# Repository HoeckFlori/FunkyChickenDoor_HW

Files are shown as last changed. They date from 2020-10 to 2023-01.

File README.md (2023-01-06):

# FunkyChickenDoor_HW

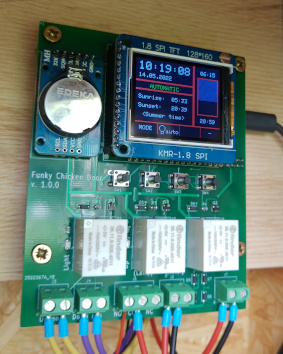
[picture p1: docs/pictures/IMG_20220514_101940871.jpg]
Hardware in mounting position


In this repository the **electronic hardware** for the 'Funky Chicken Door' [project](https://github.com/HoeckFlori/FunkyChickenDoor_SW) is/was developed.

The idea is, to develop a automatic chicken-house-door-controller and provide it on a semi-professional level with simple, available and inexpensive components. For detailed information about the features, the usage and anything else, have a look into the [corresponding software repo](https://github.com/HoeckFlori/FunkyChickenDoor_SW).

The circuit diagrams and PCB is drawn with [KiCad](https://kicad.org/) and can be opened and edited at any time with it.

You can build up the hardware as strip board solution or order a PCB from your preferred PCB dealer.  

<details>
  <summary>'development stripboard solution'</summary>

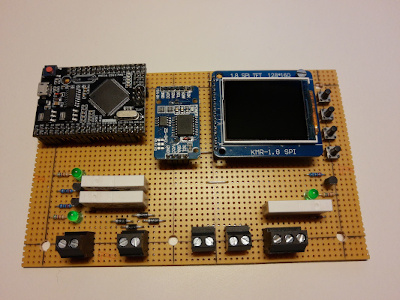
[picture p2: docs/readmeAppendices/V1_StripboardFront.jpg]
front


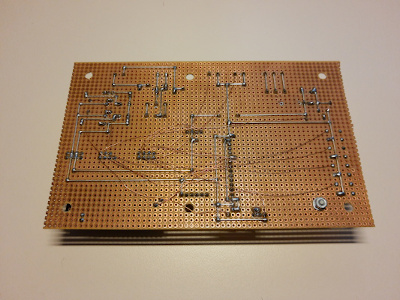
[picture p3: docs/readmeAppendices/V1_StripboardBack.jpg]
back

</details>

If you want want to use the hardware you can rebuild it for your private stuff. A BOM with the order codes to an German electronic distributor is attached. Nevertheless some 'specialized' components are needed. Look below.

In case of problems, errors or suggestions for improvement, please send me an issue.

# Quick links within the repository
## KiCad project
[KiCadProject](./AMShieldV1/ChickenDoor_V1.pro)

## Schematic
[Schematic](./AMShieldV1/ChickenDoor_V1_1-0-0_Schematic.pdf)

## Assembly print
[Assembly print](./AMShieldV1/ChickenDoor_V1_1-0-0_AssemblyPrint.pdf)

## BOM (bill of materials)
[Schematic](./AMShieldV1/ChickenDoor_V1_1-0-0_BOM_withReicheltOrderCodes.ods)

## Pictures of the PCB
<details>
  <summary>Click me to see some screenshots</summary>
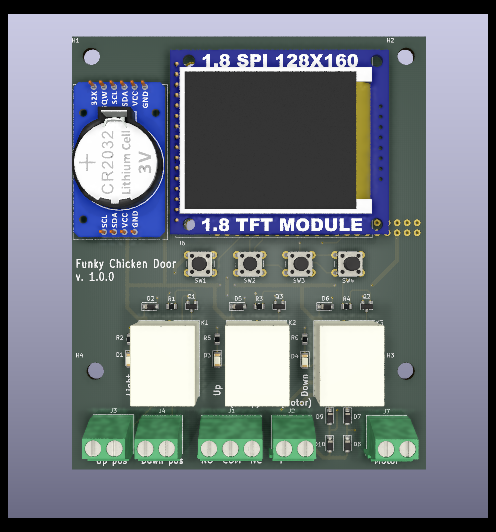
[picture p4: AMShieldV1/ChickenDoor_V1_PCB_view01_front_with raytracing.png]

  
![](./AMShieldV1/ChickenDoor_V1_PCB_view02_side%20right.png
  
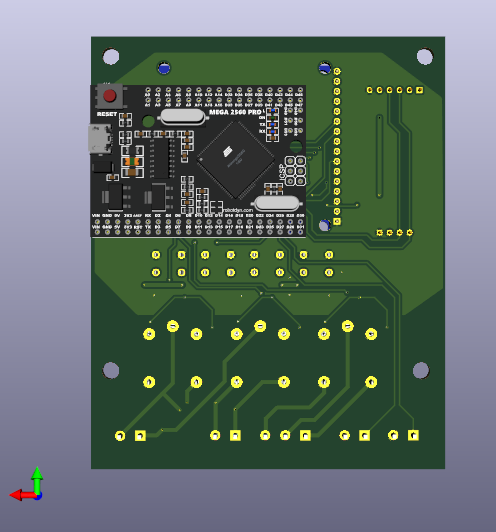
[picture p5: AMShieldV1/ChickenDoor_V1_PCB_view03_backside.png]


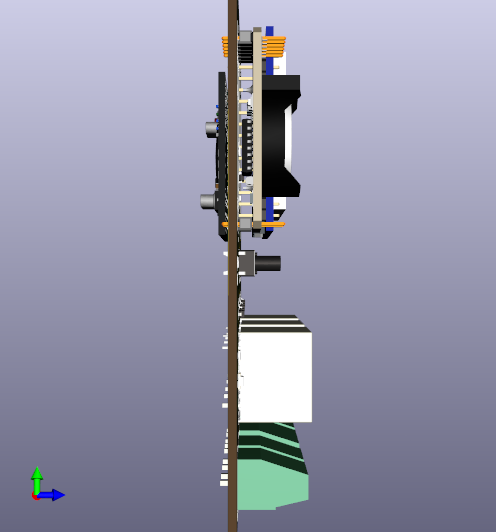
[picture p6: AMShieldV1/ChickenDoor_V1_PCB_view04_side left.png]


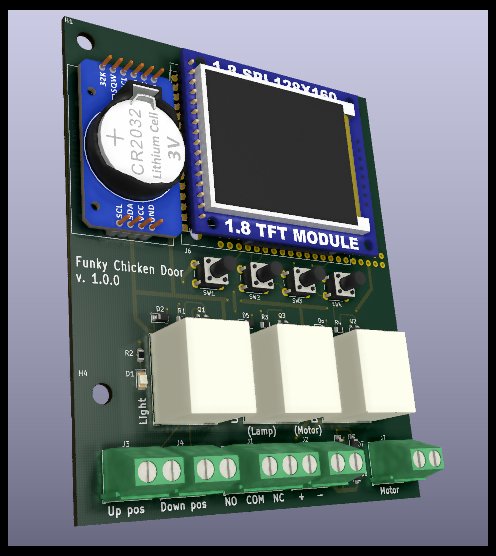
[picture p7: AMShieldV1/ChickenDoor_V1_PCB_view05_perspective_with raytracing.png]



</details>

## The more 'specialized' components you need to get

<details>
  <summary>'click me to open the list'</summary>

| What | Link to further information and (possible) vendors | Detailed information | Realistic price (from a well-known auction platform with longer shipping time), mid 2020 |
| --- | --- | --- | --- |
| MCU Board 'Mega 2560 PRO (Embed) CH340G/ATmega2560-16AU' | [https://robotdyn.com/mega-2560-pro-embed-ch340g-atmega2560-16au.html](https://robotdyn.com/mega-2560-pro-embed-ch340g-atmega2560-16au.html) or [https://www.reichelt.de/at/en/arduino-compatible-mega-2560-pro-board-ard-mega2560-pro-p299355.html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](https://www.reichelt.de/at/en/arduino-compatible-mega-2560-pro-board-ard-mega2560-pro-p299355.html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) | <ul><li>[Dimensional drawing](https://robotdyn.com/pub/media/0G-00005641==MEGA-PRO-CH340GATmega2560/DOCS/DIM==0G-00005641==MEGA-PRO-CH340GATmega2560.pdf)</li><li>[Input and Output I/O diagram](https://robotdyn.com/pub/media/0G-00005641==MEGA-PRO-CH340GATmega2560/DOCS/PINOUT==0G-00005641==MEGA-PRO-CH340GATmega2560.pdf)</li><li>[Schematic](https://robotdyn.com/pub/media/0G-00005641==MEGA-PRO-CH340GATmega2560/DOCS/Schematic==0G-00005641==MEGA-PRO-CH340GATmega2560.pdf)</li></ul> | ~ 7,- € |
| RTC DS3231 I2C AT24C32 Real Time Clock | https://www.makershop.de/module/rtc/rtc-ds3231-i2c/ | [Interface DS3231 Precision RTC Module with Arduino](https://lastminuteengineers.com/ds3231-rtc-arduino-tutorial/) | ~ 3,- € |
| 1,8 Zoll TFT LCD Display Modul 128×160 | [https://www.amazon.com/HiLetgo-ST7735R-128160-Display-Arduino/dp/B00LSG51MM](https://www.amazon.com/HiLetgo-ST7735R-128160-Display-Arduino/dp/B00LSG51MM) or [https://www.makershop.de/display/lcd-tft/waveshare-1-8inch-lcd-modul/](https://www.makershop.de/display/lcd-tft/waveshare-1-8inch-lcd-modul/) | Try to get a display like in the link! The market is full of displays of this type, but each one has other connectors, dimensions, orientations, ... .<br/> Some may interesting links:<br/> [1.8" Serial SPI 128x160 Color TFT LCD Module Display](https://www.openhacks.com/uploadsproductos/tutorial_display_tft.pdf),<br/> [https://learn.adafruit.com/1-8-tft-display/breakout-pinouts](https://learn.adafruit.com/1-8-tft-display/breakout-pinouts),<br/> [Arduino Tutorial: Making the KMR-1.8 SPI (TFT Display) work!](https://www.mschoeffler.de/2019/06/20/arduino-tutorial-making-the-kmr-1-8-spi-tft-display-work/) | ~ 8,-€ <br/> (on a well-known internet auction house) |

</details>

# FAQ
Currently nothing :smiley:

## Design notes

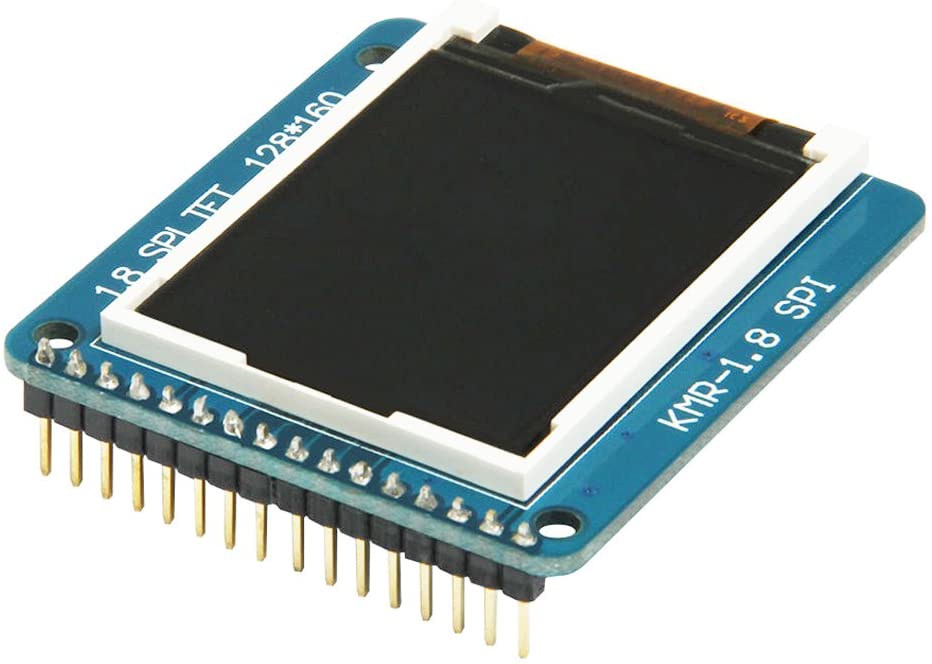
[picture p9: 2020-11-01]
docs/displayTemp/61+4ZxjomVL._AC_SL1010_.jpg

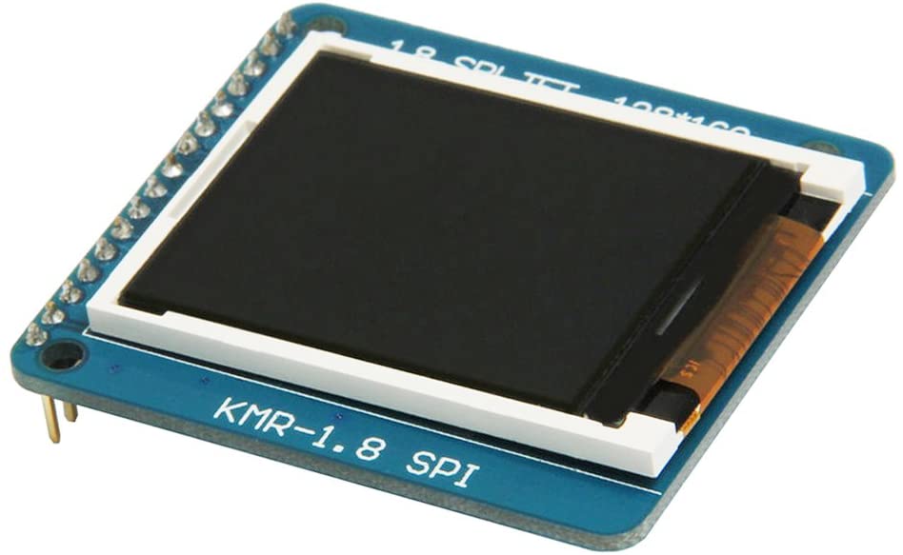
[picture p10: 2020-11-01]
docs/displayTemp/61WNY7D33nL._AC_SL1010_.jpg

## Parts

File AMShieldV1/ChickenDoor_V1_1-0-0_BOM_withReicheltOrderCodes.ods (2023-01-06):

ID | Bezeichner | Gehäuse | Stückzahl | Bezeichnung | Anbieter und Referenz | Bestellt | Reichelt Bestellnummer
1 | JP4,JP3,JP2,JP1 | SolderJumper-2_P1.3mm_Bridged_RoundedPad1.0x1.5mm | 4 | SolderJumper_2_Bridged
2 | J6 | KMR-1.8-SPI | 1 | KMR-1.8 SPI
3 | J7,J4,J3,J2 | TerminalBlock_Phoenix_MKDS-1,5-2-5.08_1x02_P5.08mm_Horizontal | 4 | Screw_Terminal_01x02 |  | x | LAKL 1,5 2 5,08
4 | J1 | TerminalBlock_Phoenix_MKDS-1,5-3-5.08_1x03_P5.08mm_Horizontal | 1 | Screw_Terminal_01x03 |  | x | LAKL 1,5 3 5,08
5 | U1 | MODULE_MEGA_PRO_EMBED_CH340G___ATMEGA2560 | 1 | MEGA_PRO_EMBED_CH340G___ATMEGA2560
6 | U2 | MODULE_TC00500_FHk_BatteryUpside | 1 | TC00500
7 | R7,R9,R4,R3,R1 | R_0805_2012Metric | 5 | 2k2 |  | x | SMD-0805 2,20K
8 | Q4 | SOT-23 | 1 | BC807 |  | x | BC 807 NXP
9 | D4,D3,D1 | LED_1206_3216Metric | 3 | LED |  |  | WUE 150120GS750
10 | Q3,Q2,Q1 | SOT-23 | 3 | BC817 |  | x | BC 817 NXP
11 | D6,D5,D2,D10,D9,D8,D7 | D_SOD-123 | 7 | 1N4448W |  | x | 1N 4448W DIO
12 | R8 | R_0805_2012Metric | 1 | 18R |  | x | SMD-0805 18,0
13 | R6,R5,R2 | R_0805_2012Metric | 3 | 560 |  | x | SMD-0805 560
14 | H4,H3,H2,H1 | MountingHole_4.3mm_M4_DIN965 | 4 | MountingHole
15 | K3,K2,K1 | Relay_SPDT_Finder_36.11 | 3 | FINDER-36.11 |  | x | FIN 36.11 5V
16 | SW4,SW3,SW2,SW1 | SW_PUSH_6mm_H9.5mm | 4 | SW_Push |  | x | TASTER 3301B

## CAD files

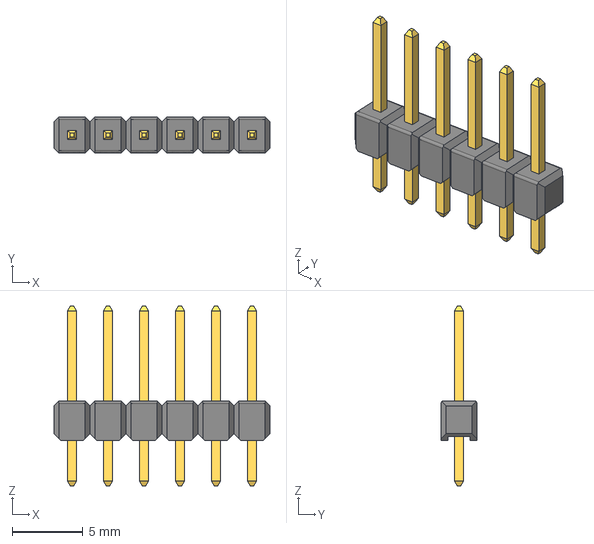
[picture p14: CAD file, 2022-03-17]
cadModels/Pin Header 1x6 TH Pitch 2.54mm.stp
15.2 x 2.54 x 12.7 mm

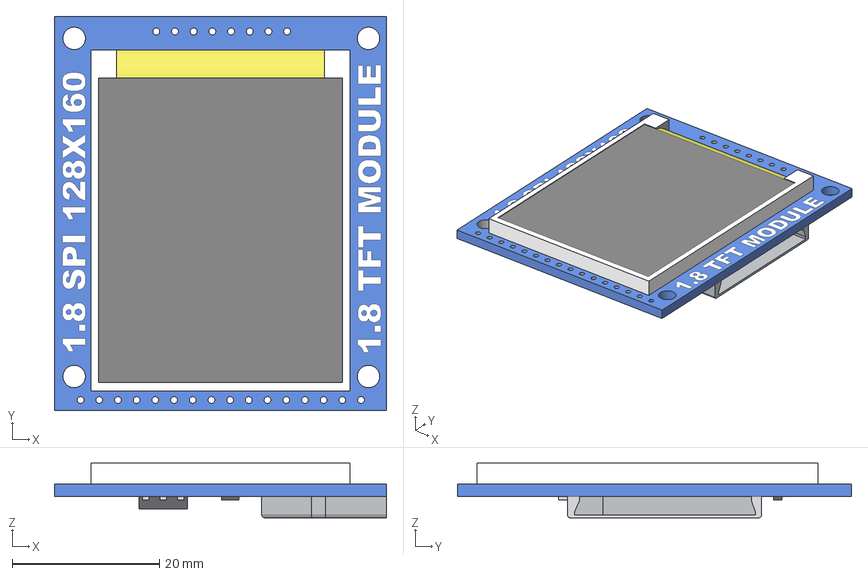
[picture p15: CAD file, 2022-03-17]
cadModels/1.8 LCD.stp
45.1 x 53.5 x 7.42 mm

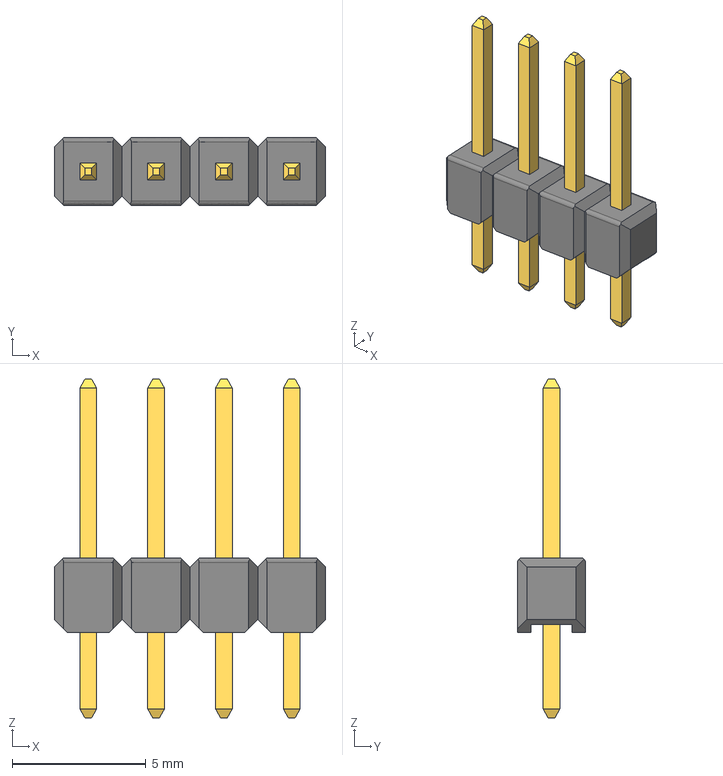
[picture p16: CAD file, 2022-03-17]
cadModels/Pin Header 1x4 TH Pitch 2.54mm.stp
10.2 x 2.54 x 12.7 mm

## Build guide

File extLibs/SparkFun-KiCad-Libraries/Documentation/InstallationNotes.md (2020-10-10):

Installation Notes
----------------

* [The KiCad site](http://kicad-pcb.org/)

**KiCad installation**

* Uninstall previous versions of KiCad
* Download KiCad stable version 4.0.5 from [http://kicad-pcb.org/download/](http://kicad-pcb.org/download/windows/) and install
* After install, you'll be prompted to install "Wings 3D", check this box to be redirected to [http://www.wings3d.com/](http://www.wings3d.com/)
* Download and install the stable release 2.1.5

**Using the libraries**

* Create a local project (this is necessary because projects hold library path information)
* Open the "Schematic Library Editor"
* Prefrences -> Component Libraries
  * Remove all libraries from list
  * Add -> navigate to SparkFun-KiCad-Libraries -> select all .lib files -> open, then hit OK
  * Test by selecting an active library.  All sparkfun libraries should be displayed.  Close the library editor
* Open the "PCB Footprint Editor"
* Preferences -> Footprint Library Manager
  * Remove all (if any) libraries, hit OK
* Preferences -> Footprint Libraries Wizard
  * Next (files on my computer)
  * Navigate to SparkFun-KiCad-Libraries -> select all .mod files and hit ok
  * Next
  * Select for this project only
  * Next
  * Close the editor
* Save the project (Green arrow into extern HDD icon, no menu exists)

Now, this project is linked to the libraries.  Open a schematic and place components.  See KiCad enginursday post for converting from schematic into board (Note: You need to have nets for this to work... not just unconnected components)

**License Information**

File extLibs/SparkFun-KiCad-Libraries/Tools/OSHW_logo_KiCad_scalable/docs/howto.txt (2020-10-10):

How to make your own:
---------------------

Watch / read this first:

* http://www.kicad-pcb.org/display/KICAD/Videos+by+zupnikal

The last two videos should be helpful for how to create a custom .emp file from images.

* http://www.re-innovation.co.uk/web12/index.php/en/blog-75/230-adding-logo-to-kicad

If you use linux (which you should), you don't have to use the online-scaler. Just use the scripts!

---

* Create a folder to hold your new footprint library.
* Copy the scripts 'make_lib.sh' and 'scale.pl' into that folder.
* Make sure these files are executable (chmod u+x ...).
* Copy your custom .emp file into that foler.

* Run the 'make_lib.sh' script as follows:

./make_lib.sh input-file.emp lib-name.mod START END

START and END are placeholders for positive integer numbers (1,2,3...) that determine
the range of created footprint sizes. The units are metric (mm).

The 'lib-name.mod' file will show up in the 'lib' sub-folder. Add it to your pcbnew
library settings as usual.

Footprints that are created for back-layers are automagically mirrored horizontally.
To place them onto a back-layer, hover the mouse-pointer over them and press 'f' for 'flip'.

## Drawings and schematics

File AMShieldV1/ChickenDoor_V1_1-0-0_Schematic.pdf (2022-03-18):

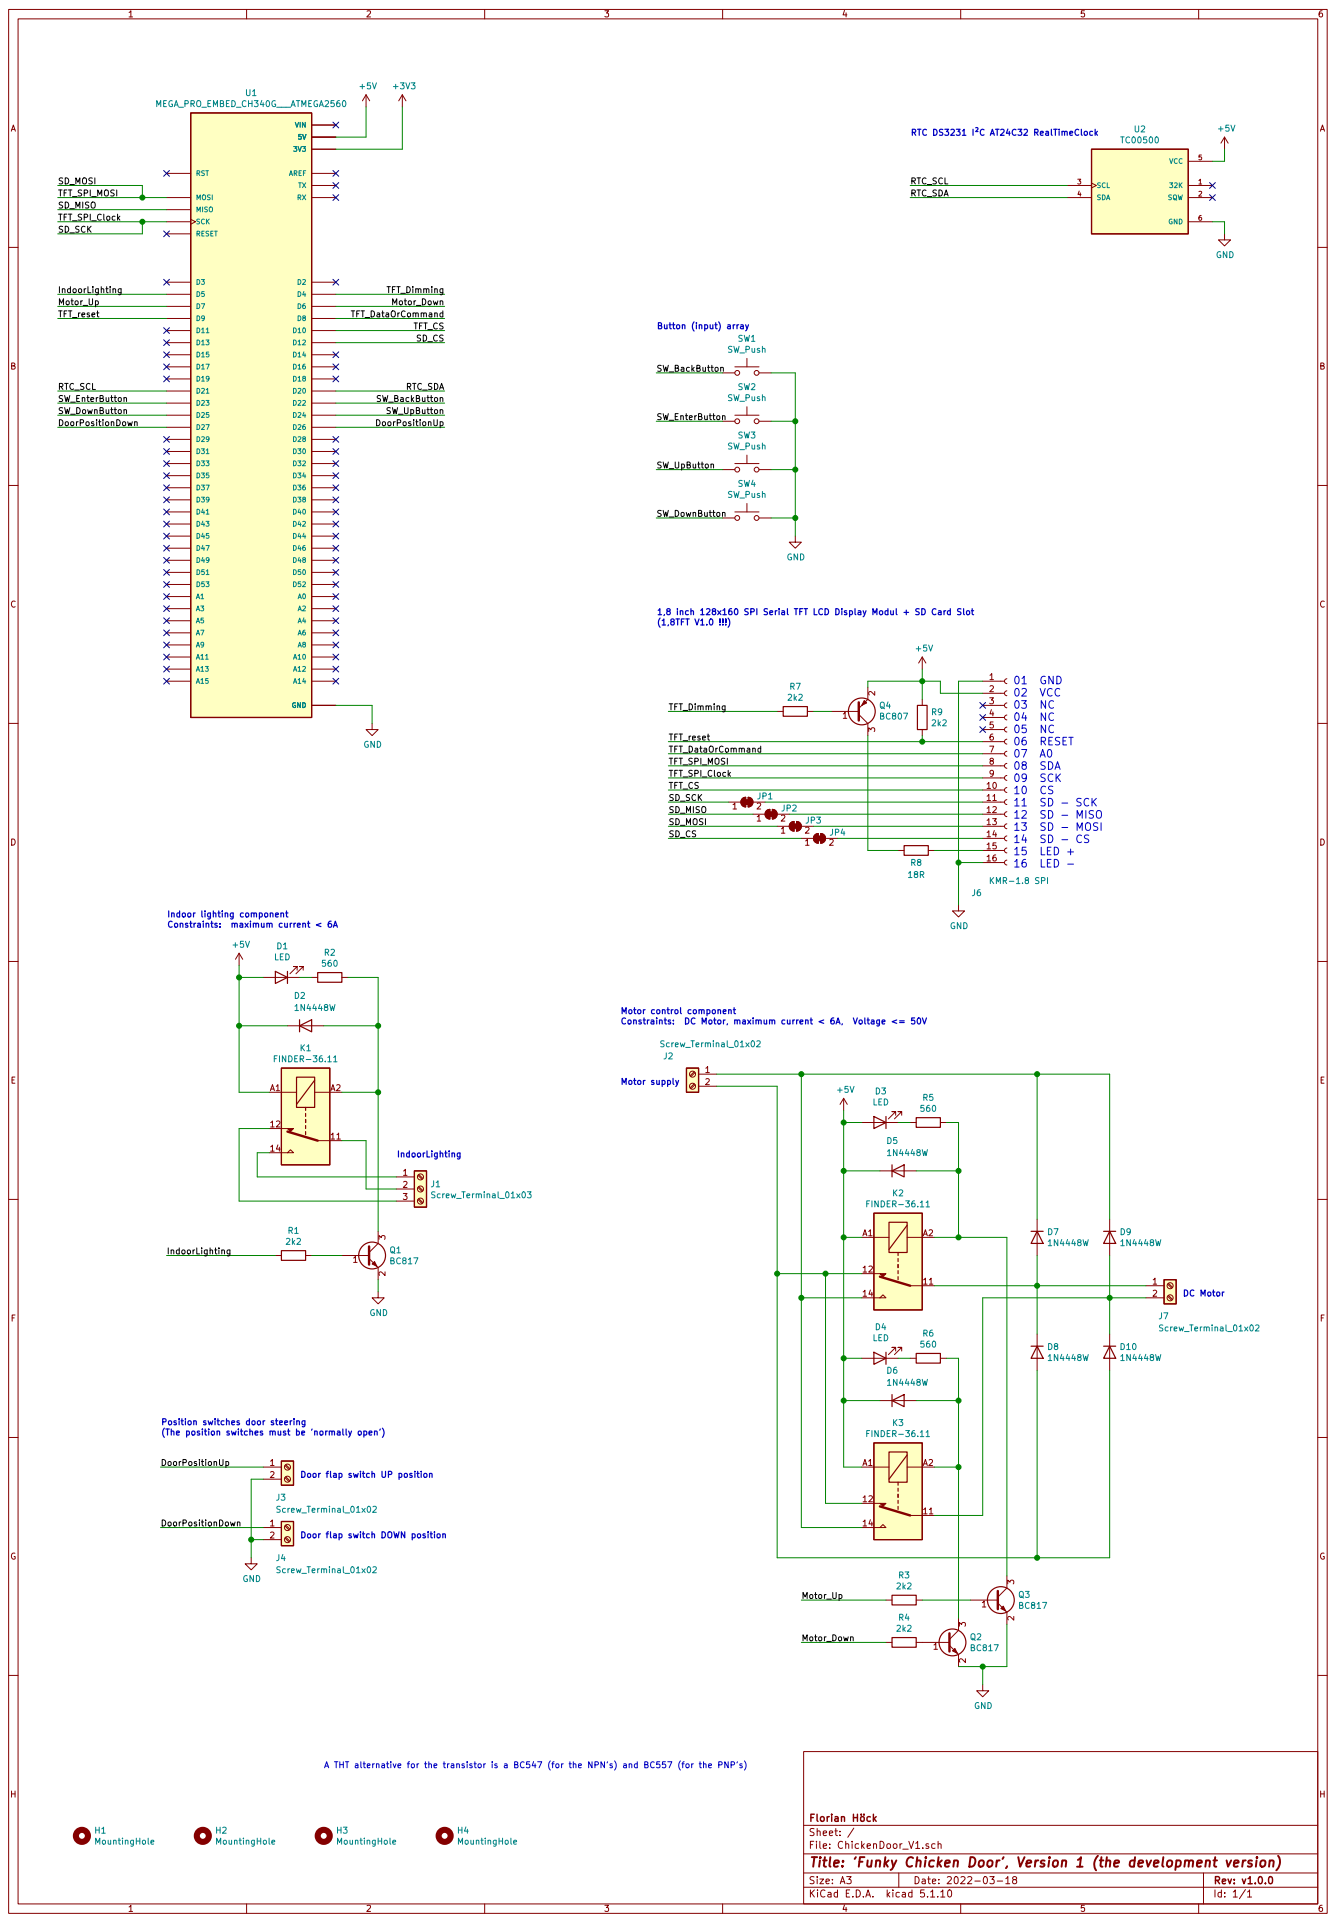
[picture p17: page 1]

1,8 inch 128x160 SPI Serial TFT LCD Display Modul + SD Card Slot
(1,8TFT V1.0 !!!)

Motor control component
Constraints: DC Motor, maximum current < 6A, Voltage <= 50V

Position switches door steering
(The position switches must be 'normally open')

A THT alternative for the transistor is a BC547 (for the NPN's) and BC557 (for the PNP's)

File: ChickenDoor_V1.sch Sheet: / Florian Höck

Id: 1/1 Title: 'Funky Chicken Door', Version 1 (the development version)

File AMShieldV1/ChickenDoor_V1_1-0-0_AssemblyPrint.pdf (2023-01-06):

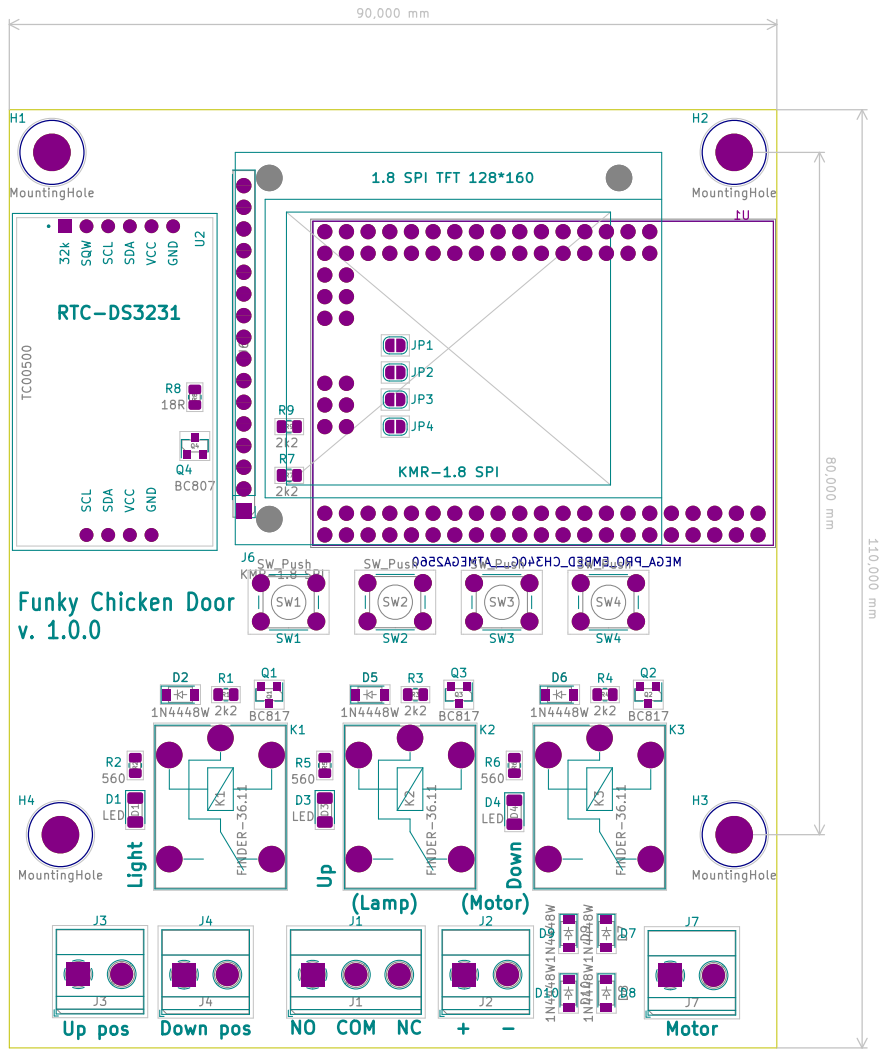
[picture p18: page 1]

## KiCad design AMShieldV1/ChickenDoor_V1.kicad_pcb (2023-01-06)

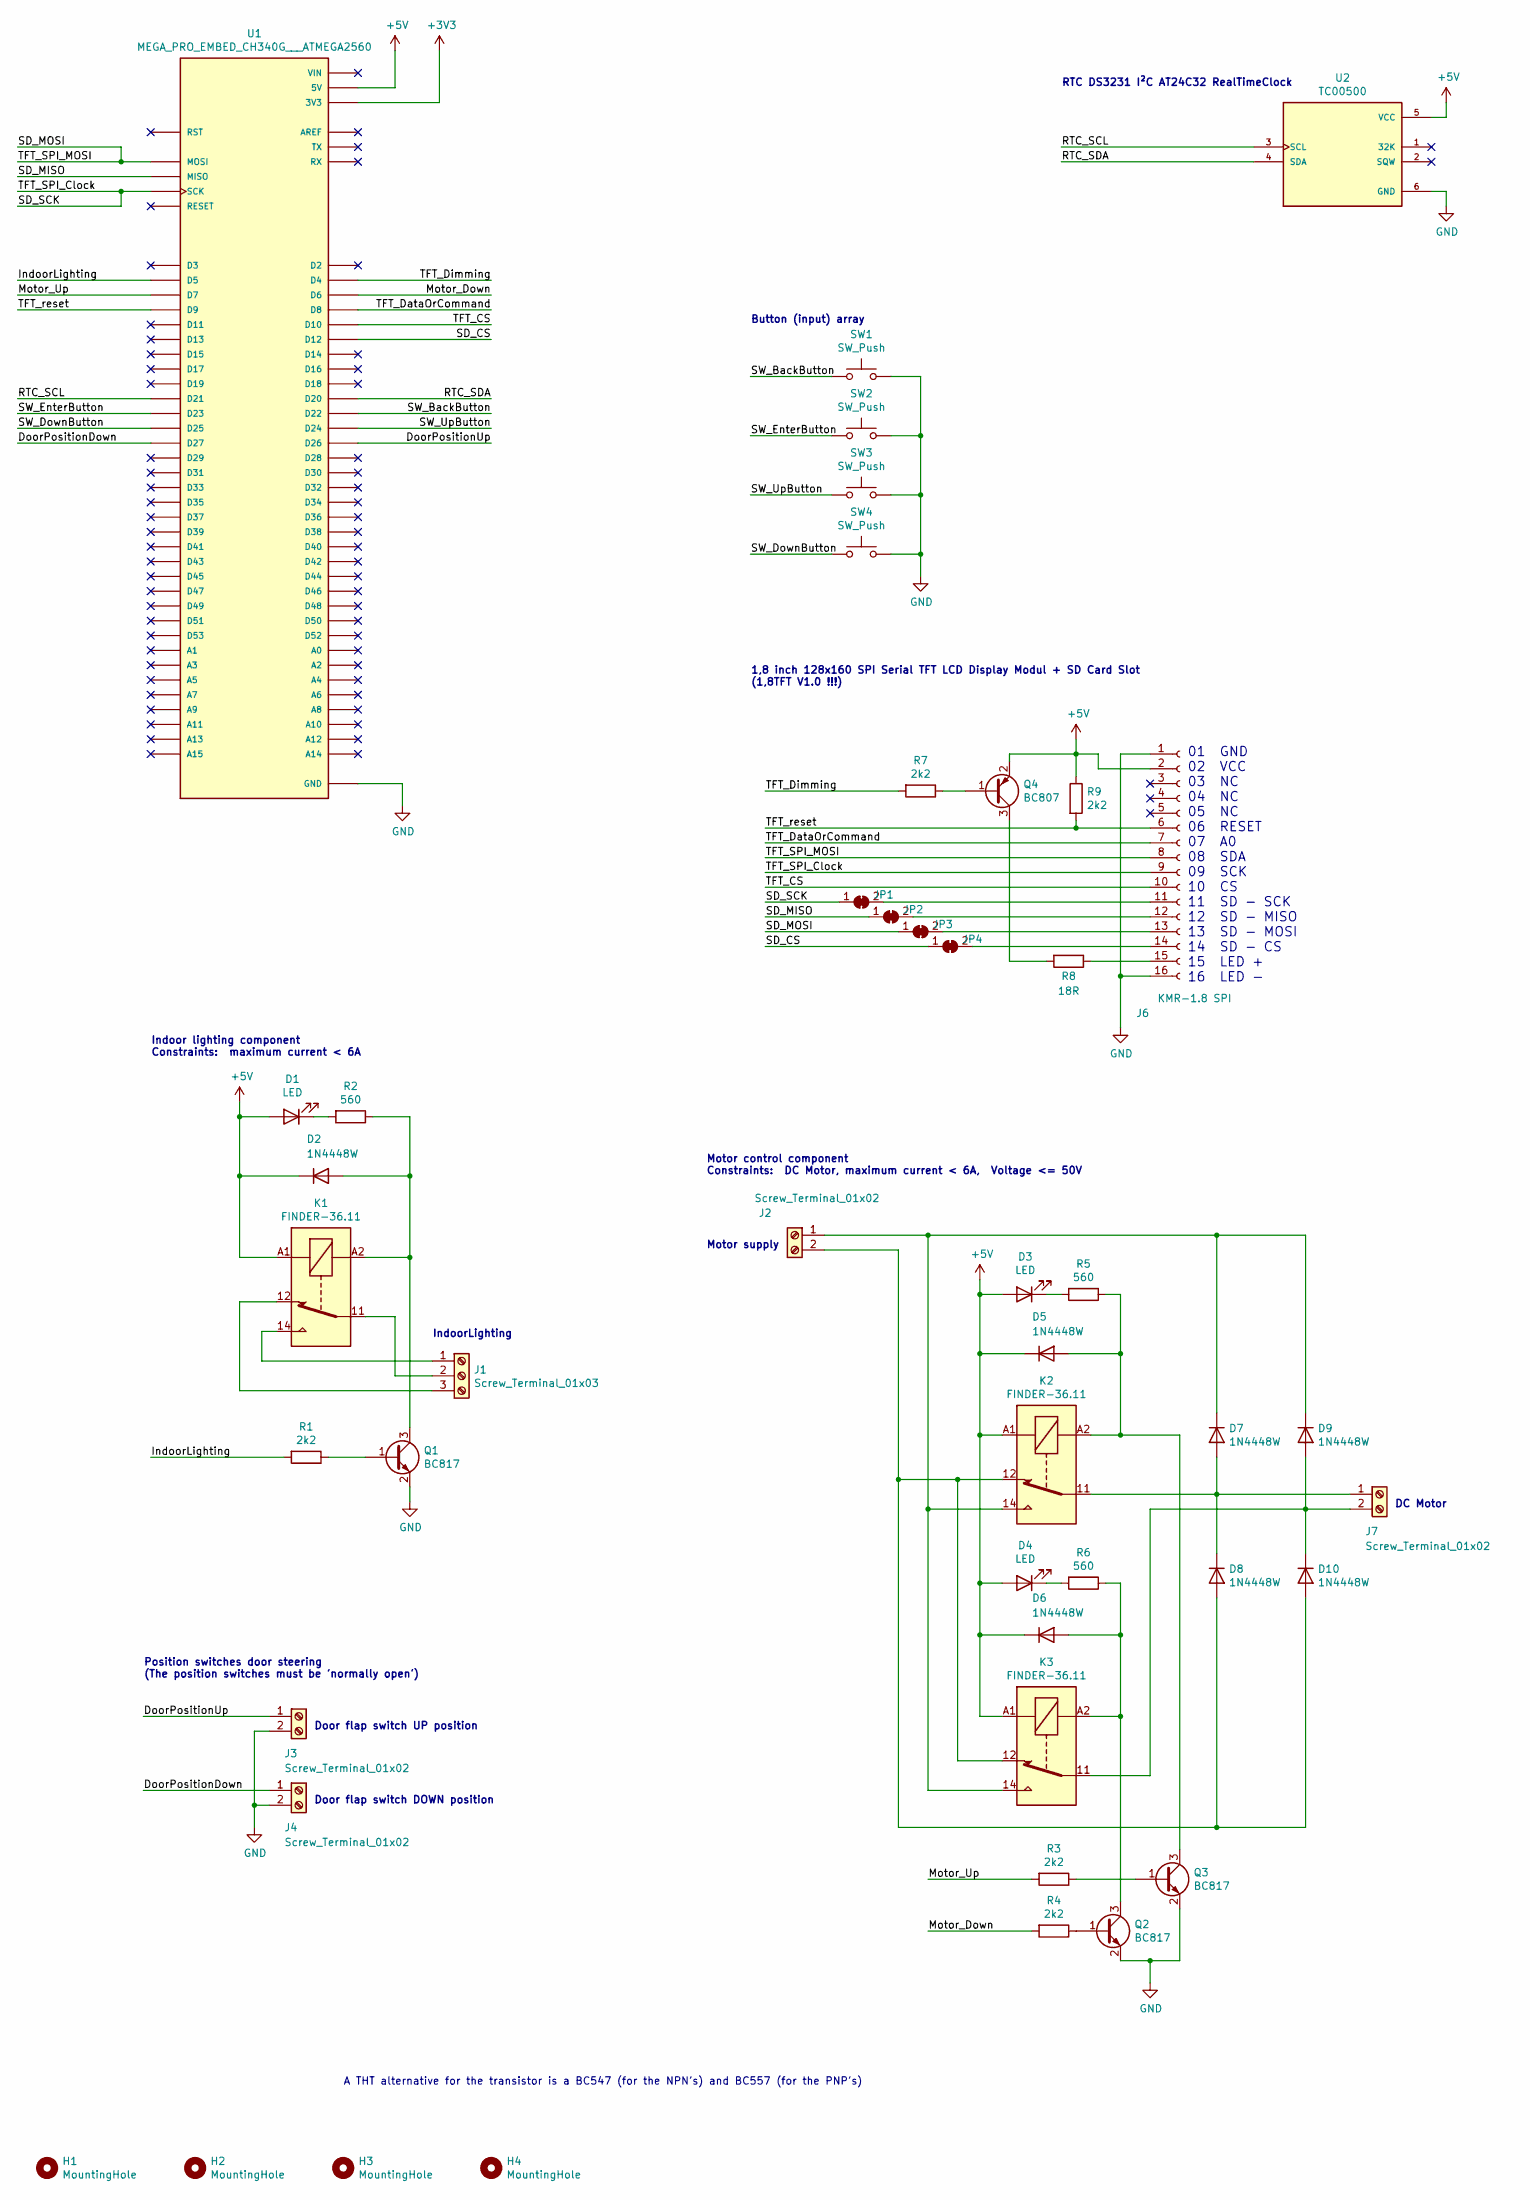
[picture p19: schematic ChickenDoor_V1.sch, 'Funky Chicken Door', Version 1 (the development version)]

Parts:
D1, D3, D4: LED; LED_1206_3216Metric
D2, D5, D6, D7, D8, D9, D10: 1N4448W; D_SOD-123
H1, H2, H3, H4: MountingHole; MountingHole_4.3mm_M4_DIN965
J1: Screw_Terminal_01x03; TerminalBlock_Phoenix_MKDS-1,5-3-5.08_1x03_P5.08mm_Horizont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
J2, J3, J4, J7: Screw_Terminal_01x02; TerminalBlock_Phoenix_MKDS-1,5-2-5.08_1x02_P5.08mm_Horizont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
J6: KMR-1.8 SPI; KMR-1.8-SPI
JP1, JP2, JP3, JP4: SolderJumper_2_Bridged; SolderJumper-2_P1.3mm_Bridged_RoundedPad1.0x1.5mm
K1, K2, K3: FINDER-36.11; Relay_SPDT_Finder_36.11
Q1, Q2, Q3: BC817; SOT-23
Q4: BC807; SOT-23
R1, R3, R4, R7, R9: 2k2; R_0805_2012Metric
R2, R5, R6: 560; R_0805_2012Metric
R8: 18R; R_0805_2012Metric
SW1, SW2, SW3, SW4: SW_Push; SW_PUSH_6mm_H9.5mm
U1: MEGA_PRO_EMBED_CH340G___ATMEGA2560; MODULE_MEGA_PRO_EMBED_CH340G___ATMEGA2560; PARTREV 12/May/2017
U2: TC00500; MODULE_TC00500_FHk_BatteryUpside; PARTREV N/A

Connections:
+3V3: U1.3V3_1 (3V3), U1.3V3_2 (3V3)
+5V: D1.2 (A), D2.1 (K), D3.2 (A), D4.2 (A), D5.1 (K), D6.1 (K), J6.2, K1.A1, K2.A1, K3.A1, Q4.2 (E), R9.1, U1.5V_1 (5V), U1.5V_2 (5V), U1.5V_3 (5V), U2.5 (VCC)
/DoorPositionDown: J4.1, U1.D27
/DoorPositionUp: J3.1, U1.D26
/IndoorLighting: R1.2, U1.D5
/Motor_Down: R4.2, U1.D6
/Motor_Up: R3.2, U1.D7
/RTC_SCL: U1.D21, U2.3 (SCL)
/RTC_SDA: U1.D20, U2.4 (SDA)
/SD_CS: JP4.1 (A), U1.D12
/SD_MISO: JP2.1 (A), U1.MISO
/SD_MOSI: J6.8, JP3.1 (A), U1.MOSI
/SD_SCK: J6.9, JP1.1 (A), U1.SCK
/SW_BackButton: SW1.1, U1.D22
/SW_DownButton: SW4.1, U1.D25
/SW_EnterButton: SW2.1, U1.D23
/SW_UpButton: SW3.1, U1.D24
/TFT_CS: J6.10, U1.D10
/TFT_DataOrCommand: J6.7, U1.D8
/TFT_Dimming: R7.2, U1.D4
/TFT_reset: J6.6, R9.2, U1.D9
GND: J3.2, J4.2, J6.1, J6.16, Q1.2 (E), Q2.2 (E), Q3.2 (E), SW1.2, SW2.2, SW3.2, SW4.2, U1.GND_1 (GND), U1.GND_2 (GND), U1.GND_3 (GND), U2.6 (GND)
unnamed: D1.1 (K), R2.2
unnamed: D2.2 (A), K1.A2, Q1.3 (C), R2.1
unnamed: D3.1 (K), R5.2
unnamed: D4.1 (K), R6.2
unnamed: D5.2 (A), K2.A2, Q3.3 (C), R5.1
unnamed: D6.2 (A), K3.A2, Q2.3 (C), R6.1
unnamed: D7.1 (K), D9.1 (K), J2.1, K2.14, K3.14
unnamed: D7.2 (A), D8.1 (K), J7.1, K2.11
unnamed: D9.2 (A), D10.1 (K), J7.2, K3.11
unnamed: D8.2 (A), D10.2 (A), J2.2, K2.12, K3.12
unnamed: J1.1, K1.14
unnamed: J1.2, K1.11
unnamed: J1.3, K1.12
unnamed: J6.11, JP1.2 (B)
unnamed: J6.12, JP2.2 (B)
unnamed: J6.13, JP3.2 (B)
unnamed: J6.14, JP4.2 (B)
unnamed: J6.15, R8.1
unnamed: Q1.1 (B), R1.1
unnamed: Q2.1 (B), R4.1
unnamed: Q3.1 (B), R3.1
unnamed: Q4.1 (B), R7.1
unnamed: Q4.3 (C), R8.2
unnamed: U1.VIN_1 (VIN), U1.VIN_2 (VIN)

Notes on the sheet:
01 GND 02 VCC 03 NC 04 NC 05 NC 06 RESET 07 A0 08 SDA 09 SCK 10 CS 11 SD - SCK 12 SD - MISO 13 SD - MOSI 14 SD - CS 15 LED + 16 LED -
1,8 inch 128x160 SPI Serial TFT LCD Display Modul + SD Card Slot (1,8TFT V1.0 !!!)
RTC DS3231 I²C AT24C32 RealTimeClock
DC Motor
Motor supply
Door flap switch UP position
Door flap switch DOWN position
IndoorLighting
Button (input) array
Motor control component Constraints: DC Motor, maximum current < 6A, Voltage <= 50V
Indoor lighting component Constraints: maximum current < 6A
Position switches door steering (The position switches must be 'normally open')
A THT alternative for the transistor is a BC547 (for the NPN's) and BC557 (for the PNP's)

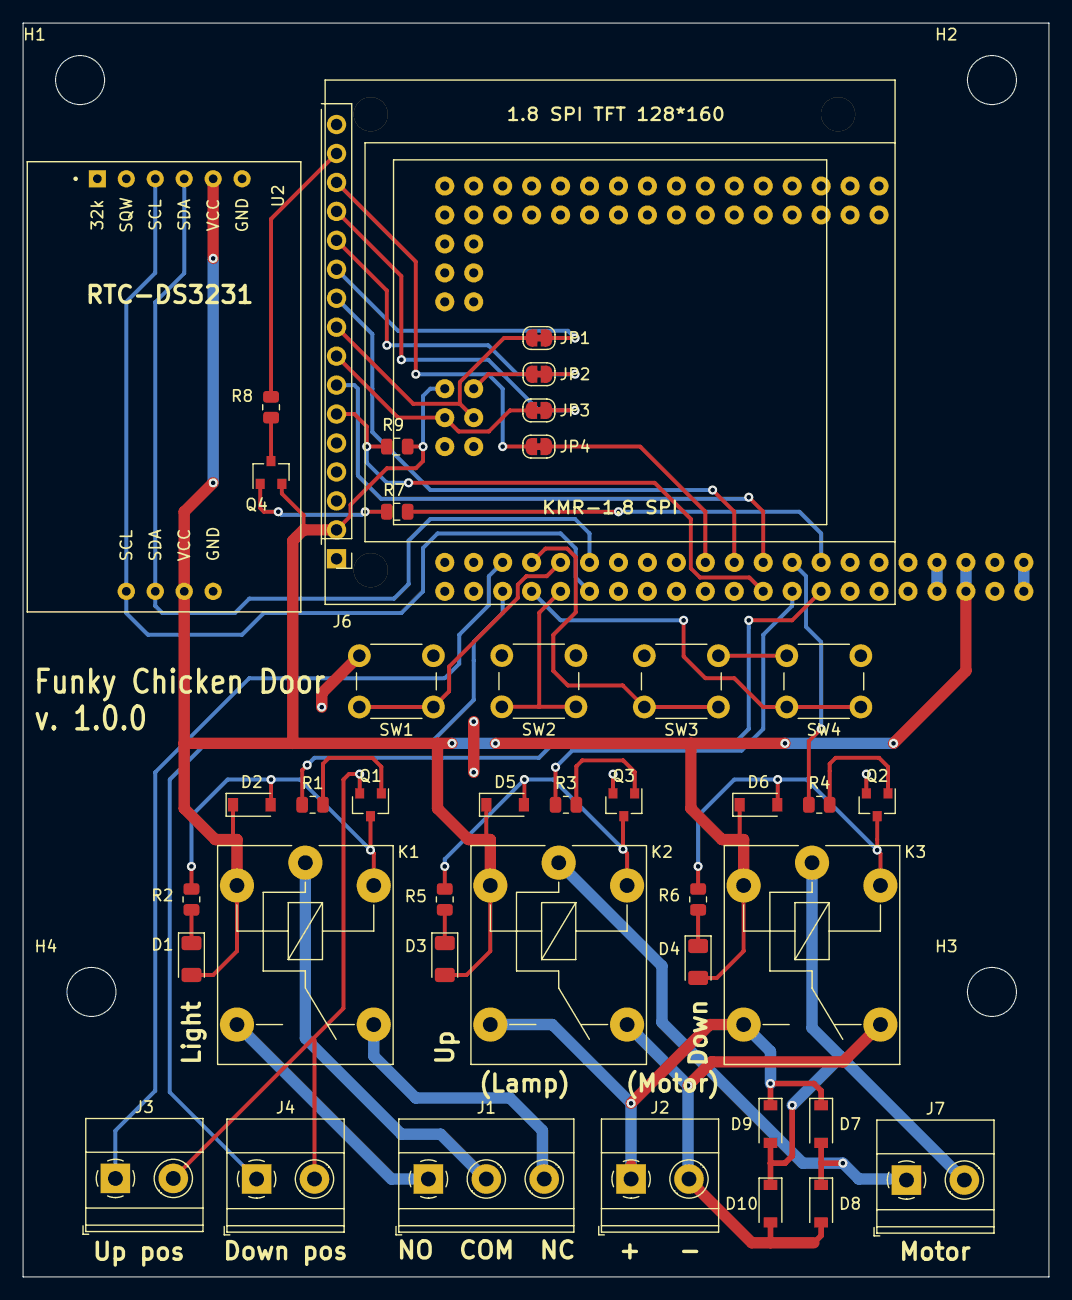
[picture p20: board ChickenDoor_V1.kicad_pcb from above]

Board: 2 copper layers, 90.0 x 110.0 mm, 46 parts (1 on the bottom side), 46 nets.

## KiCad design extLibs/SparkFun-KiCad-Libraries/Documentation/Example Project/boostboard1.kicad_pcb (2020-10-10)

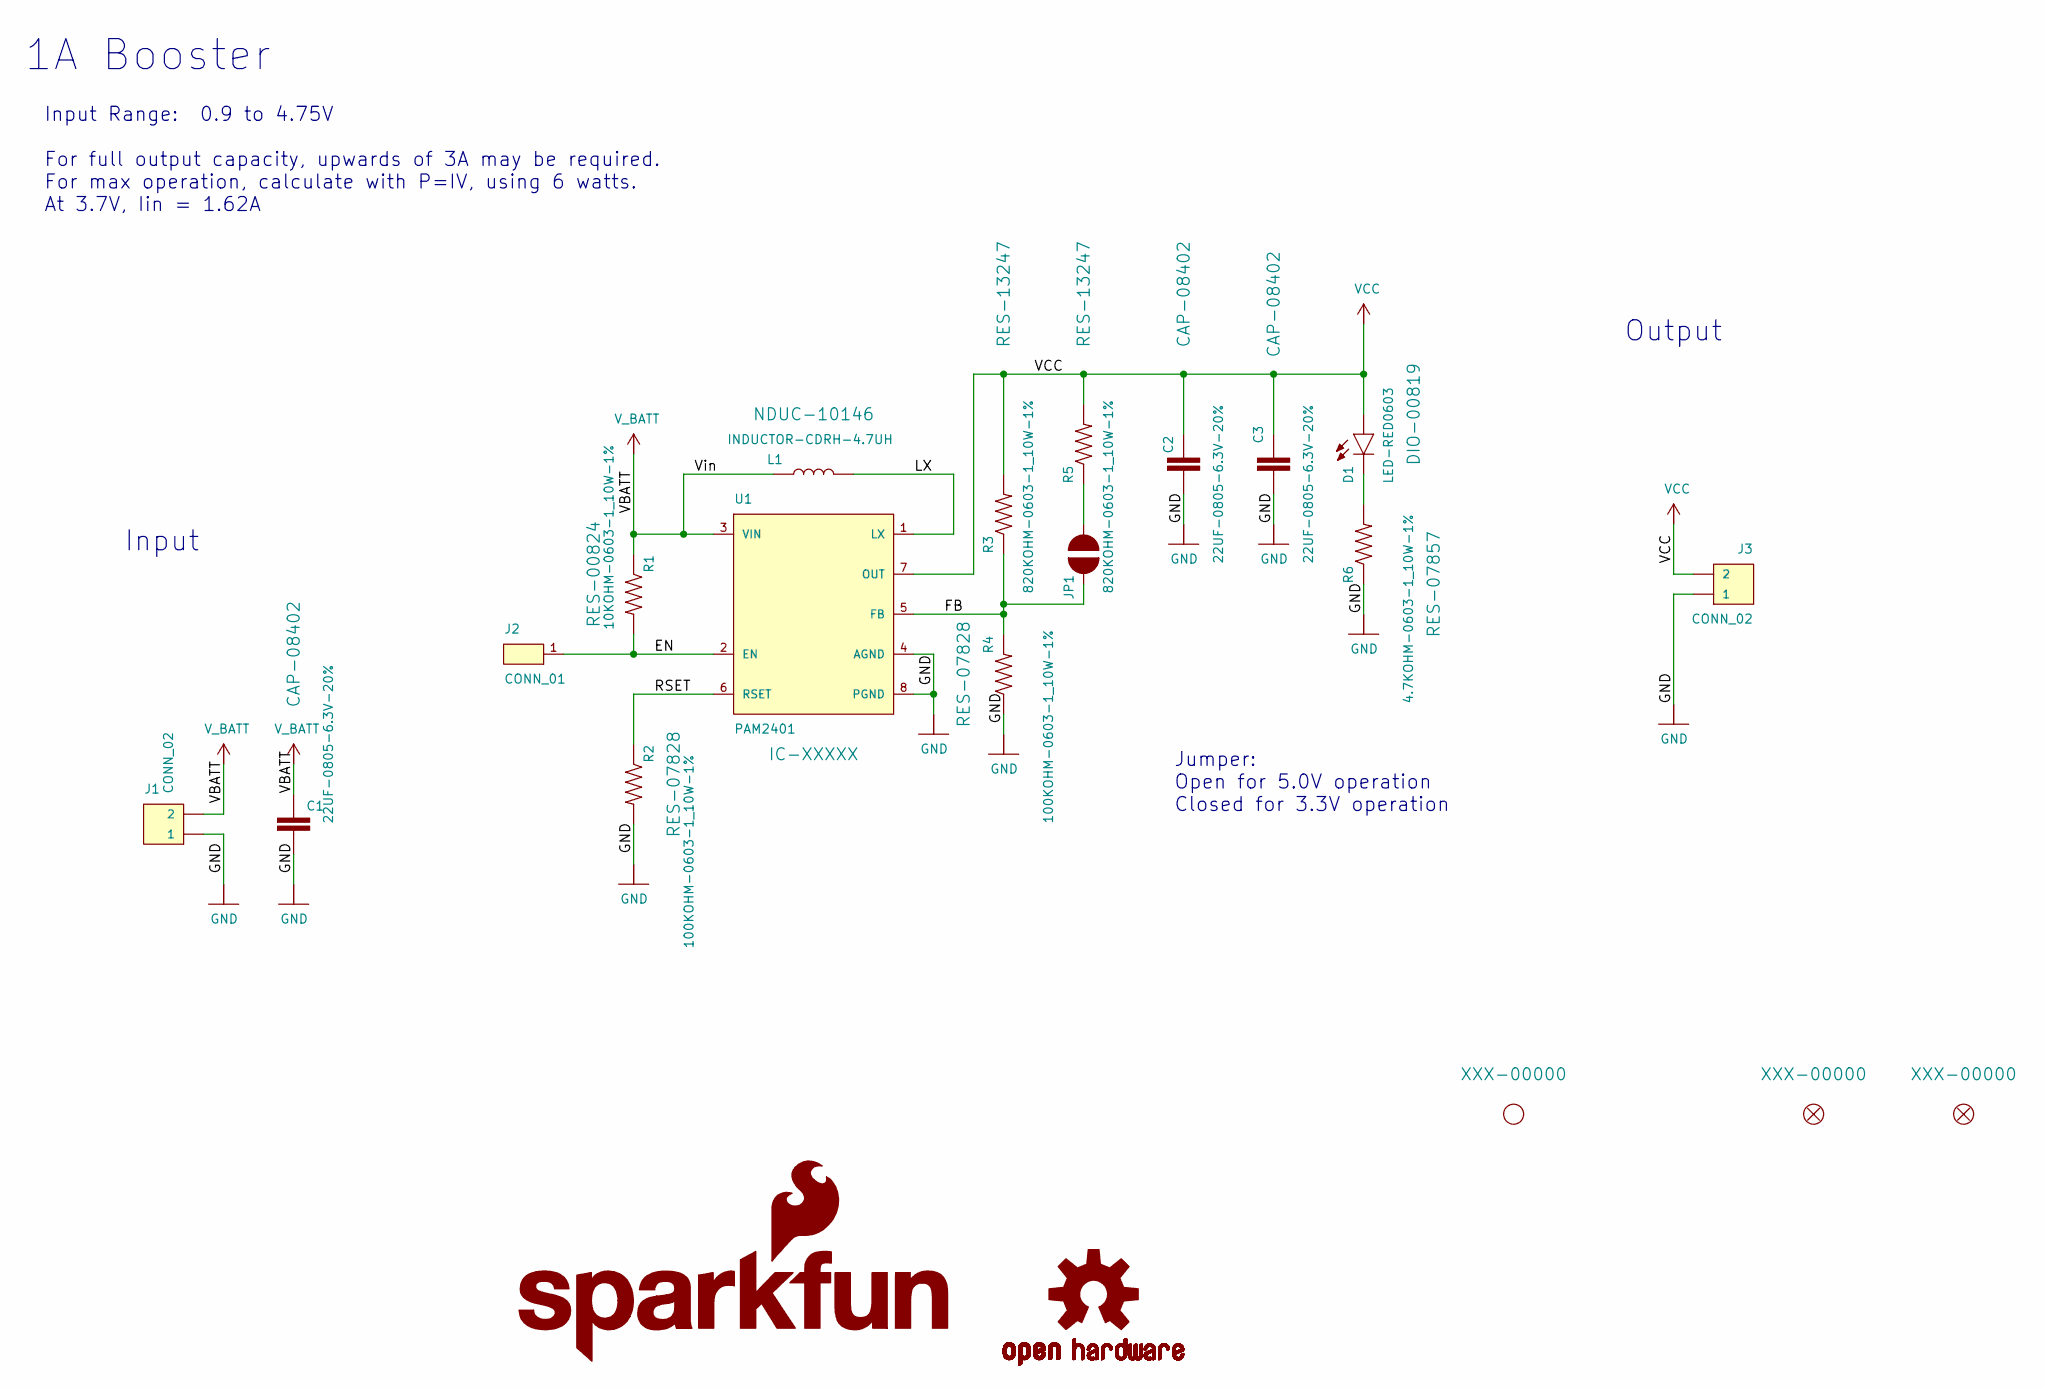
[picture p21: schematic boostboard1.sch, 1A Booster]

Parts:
C1, C2, C3: 22UF-0805-6.3V-20%; 0805
D1: LED-RED0603; LED-0603
FD1, FD2: FIDUCIAL1X2; FIDUCIAL-1X2
H1: STAND-OFF
J1, J3: CONN_02; 1X02
J2: CONN_01; 1X01
JP1: JUMPER-SMT_2_NO; SMT-JUMPER_2_NO_SILK
L1: INDUCTOR-CDRH-4.7UH; INDUCTOR_2.2UH
LOGO1: SFE_LOGO_NAME_FLAME.1_INCH; SFE_LOGO_NAME_FLAME_.1
LOGO2: OSHW-LOGOS; OSHW-LOGO-S
R1: 10KOHM-0603-1_10W-1%; 0603
R2, R4: 100KOHM-0603-1_10W-1%; 0603
R3, R5: 820KOHM-0603-1_10W-1%; 0603
R6: 4.7KOHM-0603-1_10W-1%; 0603
U1: PAM2401; MSOP8

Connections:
/EN: J2.1, R1.2, U1.2 (EN)
/FB: JP1.2, R3.1, R4.2, U1.5 (FB)
/GND: C1.2, C2.2, C3.2, J1.1, J3.1, R2.2, R4.1, R6.1, U1.4 (AGND), U1.8 (PGND)
/LX: L1.P$2 (2), U1.1 (LX)
/RSET: R2.1, U1.6 (RSET)
/VBATT: C1.1, J1.2, L1.P$1 (1), R1.1, U1.3 (VIN)
/VCC: C2.1, C3.1, D1.A, J3.2, R3.2, R5.2, U1.7 (OUT)
unnamed: D1.C, R6.2
unnamed: JP1.1, R5.1

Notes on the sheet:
1A Booster
Jumper: Open for 5.0V operation Closed for 3.3V operation
Input
Output
Input Range: 0.9 to 4.75V For full output capacity, upwards of 3A may be required. For max operation, calculate with P=IV, using 6 watts. At 3.7V, Iin = 1.62A

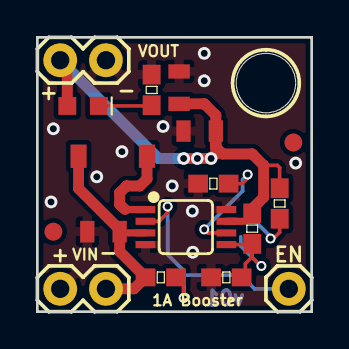
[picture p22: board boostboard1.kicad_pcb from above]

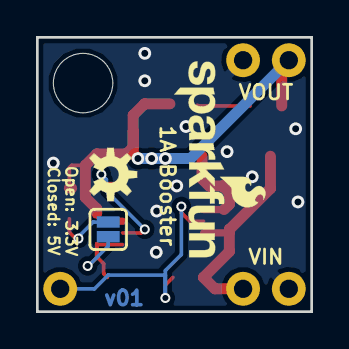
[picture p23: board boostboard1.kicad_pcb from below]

Board: 2 copper layers, 15.2 x 15.2 mm, 21 parts (3 on the bottom side), 9 nets.

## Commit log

2020-10-10 Initial commit with the preliminary work from the existing software repository.
    [ChickenDoor_V1.kicad_pcb, ChickenDoor_V1.sch, _saved_boostboard1.sch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]
2020-11-01 Built up the stripboard solution. Minor changes in the circuit. Updated the readme.
    [ARDUINO MEGA 2560 MINI 2_2020-10-16_20-42-19.pcbdoc, ARDUINO MEGA 2560 MINI 2_2020-10-16_20-43-03.dxf, ChickenDoor_V1.kicad_pcb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]
2022-03-17 First draft of the PCB with updated schematic.
    [1.8 LCD.stp, ARDUINO MEGA 2560 MINI 2_2020-10-16_20-42-19.pcbdoc, ARDUINO MEGA 2560 MINI 2_2020-10-16_20-43-03.dxf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]
2022-03-18 All manufacturing documents added. Order sent.
    [ChickenDoor_V1-B_Cu.gbr, ChickenDoor_V1-B_Mask.gbr, ChickenDoor_V1-B_Paste.gbr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]
2022-03-25 Minor addition to the BOM. Some cleanups.
    [ChickenDoor_V1_1-0-0_BOM.csv, ChickenDoor_V1_1-0-0_BOM_withReicheltOrderCodes.ods]
2023-01-06 Finalized docu
    [ChickenDoor_V1.kicad_pcb, ChickenDoor_V1_1-0-0_BOM_withReicheltOrderCodes.ods]

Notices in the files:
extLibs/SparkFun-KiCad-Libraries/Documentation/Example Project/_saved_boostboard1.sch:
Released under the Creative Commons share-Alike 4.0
